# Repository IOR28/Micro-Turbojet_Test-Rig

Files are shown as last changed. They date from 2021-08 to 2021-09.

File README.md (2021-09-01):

# Micro-Turbojet Test Rig

This repository contains all the files created during my thesis, Test Rig Design for a Micro-Turbojet Engine. More information about these contents, designs and uses can be found in the document of the thesis.

Different parts of the test rig design where explored during the project, these are sepparated into folders with the same topic. The explanation of this organization and a brief explanation of each subproject can be found below.

### Contents

+ [StructureDesign](#structuredesign): Autodesk Inventor project
	+ Bellmouth: Parts, drawings and final files
	+ CommercialParts
	+ DesignedParts: Parts and drawings
+ [DataAcquisitionMCs](#dataacquisitionmcs): MPLAB X projects
	+ Pressure
	+ Temperature
	+ Thrust_Flow
+ [DataProcessingMaster](#dataprocessingmaster): Python files and classes
+ [PCBDesigns](#pcbdesigns): Autodesk Eagle projects
	+ RTD_conditioning
	+ System_control
	+ General_board

## [StructureDesign](./StructureDesign)

This folder contains the Autodesk Inventor files of the designed bench. the bench features both [commercial parts](./StructureDesign/CommercialParts) and [designed parts](./StructureDesign/DesignedParts). The design of a [bellmouth](./StructureDesign/Bellmouth) is also included.

All the designed components have their corresponding sketches in DWG, DXF and PDF formats so that they can be manufactured. The bellmouth is expected to be 3D printed, therefore, STL files are profided along with the sketches. The links to the commercial parts can be found in the budget of the project (document).

## [DataAcquisitionMCs](./DataAcquisitionMCs)

Here the MPLAB X projects can be found. Files are coded in C and are divided into 3 projects (each one corresponding to a microcontroller):
+ Pressure
+ Temperature
+ Thrust_Flow

In order to program the microcontrollers it is necessary to open the projects in the MPLAB X IDE, compile them and then transfer them to the mCs through a USB cable.

## [DataProcessingMaster](./DataProcessingMaster)

This folder contains the Python files and classes necessary to program the Raspberry Pi 4 that acts as master. This master connects to the microcontrollers in order to gather data and save it to a database.

All the files must be saved into the `Turbojet` folder (as they are organized) inside the Raspberry Pi 4 in order to function properly. More information about how the program works and how to modify it can be found in the document.

## [PCBDesigns](./PCBDesigns)

Three boards are designed to hold all the electronics together. Autodesk Eagle is used to create these and their projects can be found inside this folder. Boards are:
+ An RTD PT100 circuit board
+ A control board
+ A base board to hold all conditioning boards

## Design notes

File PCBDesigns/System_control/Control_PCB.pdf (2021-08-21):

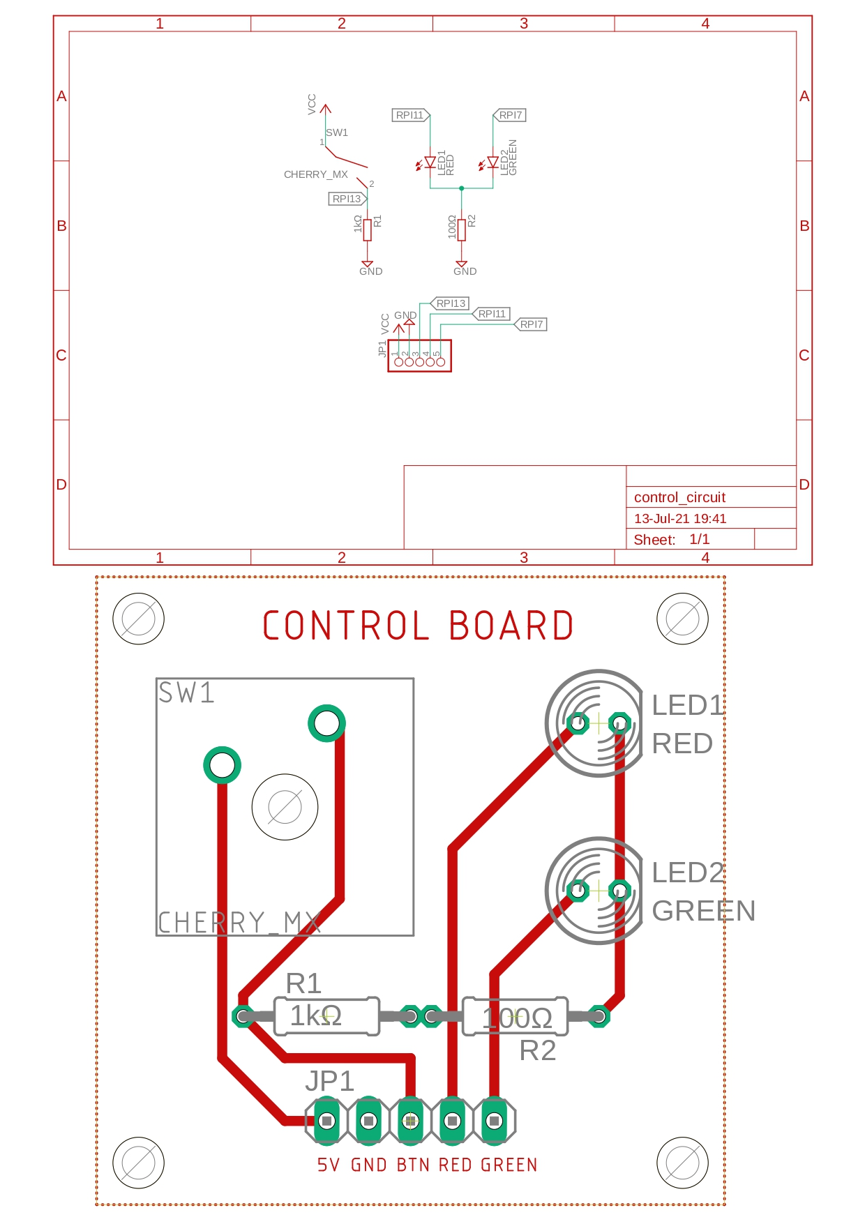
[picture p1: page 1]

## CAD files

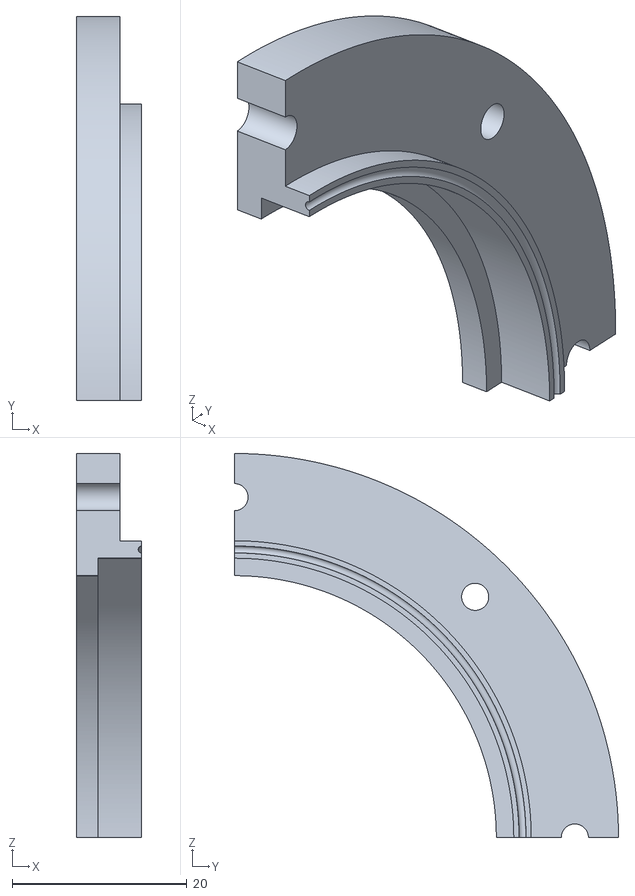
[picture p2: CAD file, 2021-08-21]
StructureDesign/Bellmouth/3DPrint/testprint_connector.stl
7.50 x 44.0 x 44.0

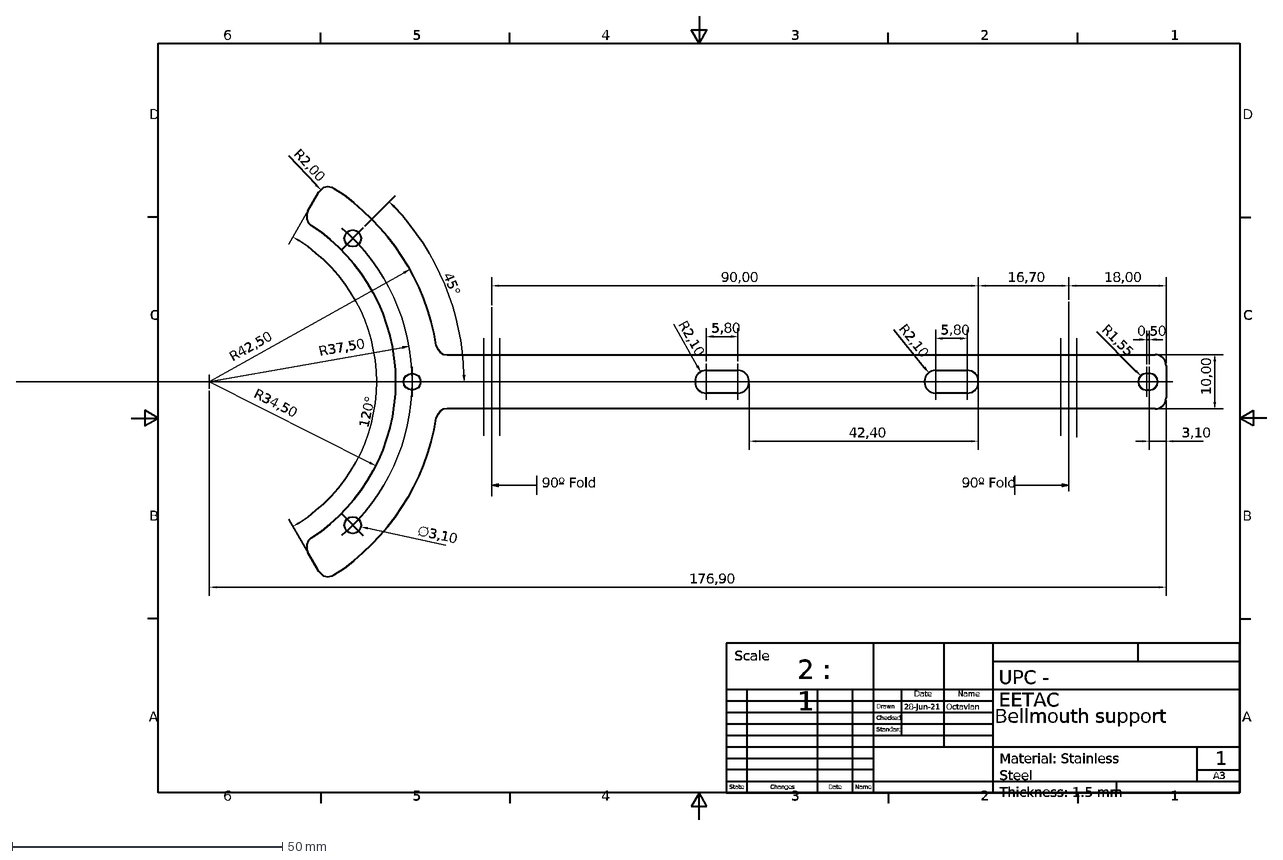
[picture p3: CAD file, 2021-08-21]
StructureDesign/Bellmouth/Drawings/DXF/Bellmouth_union.dxf
1
2
3
4
5
6
A
B
C
D
A3
Bellmouth support
28-Jun-21
Octavian
State
Changes
Date
Name
Drawn
Checked
Standard
5,80
120°
R34,50
R37,50
R42,50
45°
10,00
18,00
176,90
R2,10
3,10
0,50
R1,55
R2,00
∅3,10
90,00
16,70
42,40
Scale
2 : 1
UPC - EETAC
Material: Stainless Steel Thickness: 1.5 mm
90º Fold

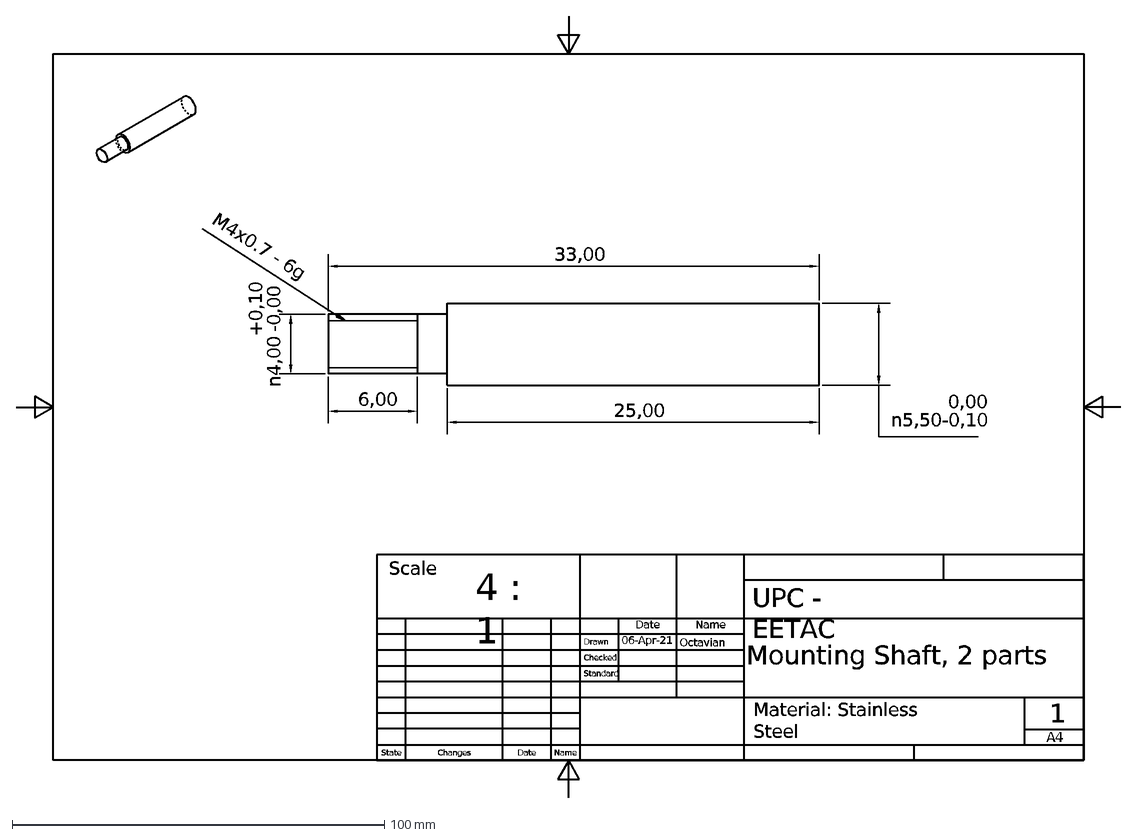
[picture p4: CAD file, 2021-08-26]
StructureDesign/DesignedParts/Drawings/DXF/Mounting_Shaft.dxf
1
A4
Mounting Shaft, 2 parts
06-Apr-21
Octavian
State
Changes
Date
Name
Drawn
Checked
Standard
33,00
25,00
6,00
M4x0.7 - 6g
Scale
4 : 1
UPC - EETAC
Material: Stainless Steel

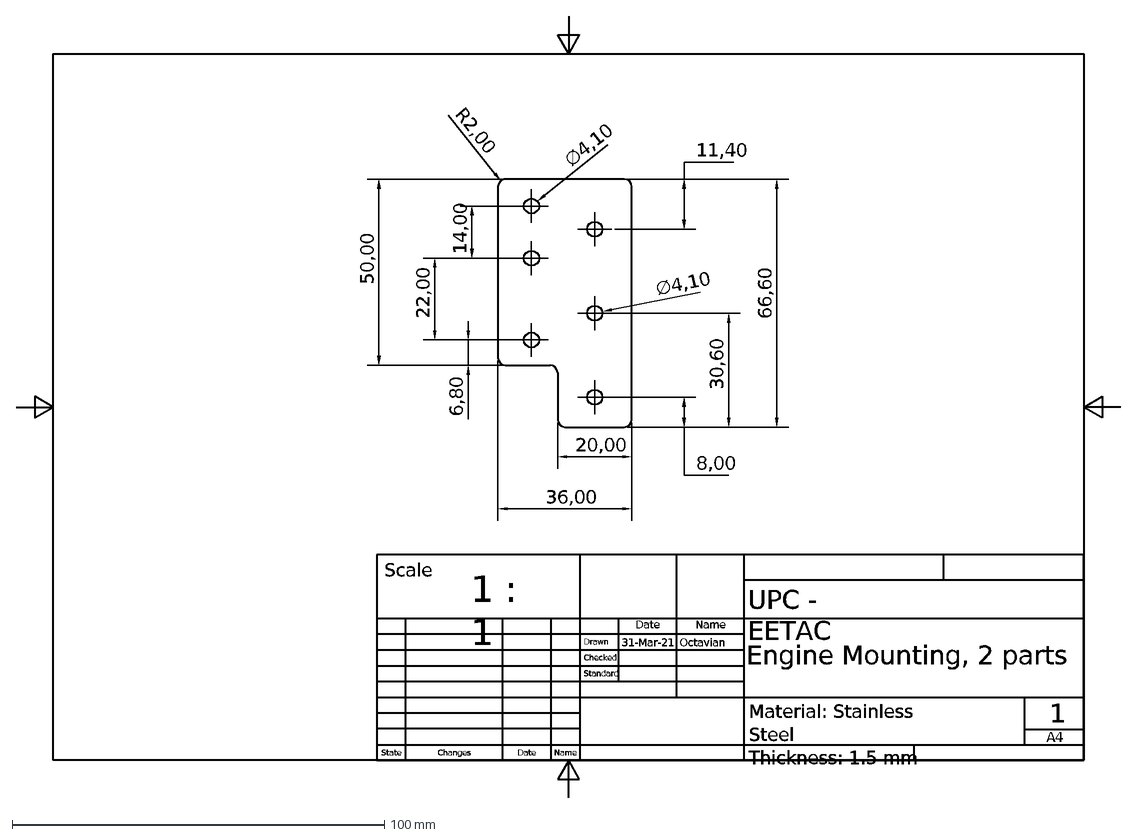
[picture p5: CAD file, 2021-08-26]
StructureDesign/DesignedParts/Drawings/DXF/Engine_Mounting.dxf
1
A4
Engine Mounting, 2 parts
31-Mar-21
Octavian
State
Changes
Date
Name
Drawn
Checked
Standard
66,60
50,00
R2,00
14,00
22,00
36,00
20,00
6,80
11,40
∅4,10
30,60
8,00
Scale
1 : 1
UPC - EETAC
Material: Stainless Steel Thickness: 1.5 mm

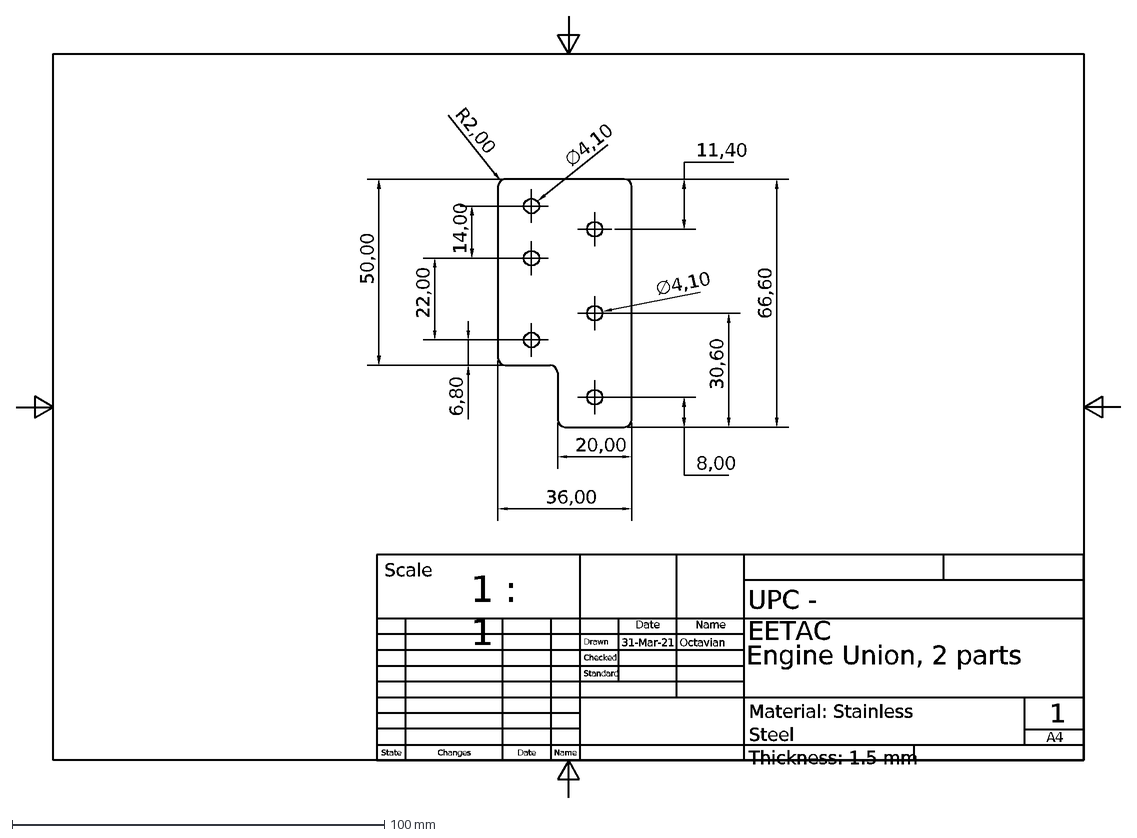
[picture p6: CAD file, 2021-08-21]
StructureDesign/DesignedParts/Drawings/DXF/Engine_Union.dxf
1
A4
Engine Union, 2 parts
31-Mar-21
Octavian
State
Changes
Date
Name
Drawn
Checked
Standard
66,60
50,00
R2,00
14,00
22,00
36,00
20,00
6,80
11,40
∅4,10
30,60
8,00
Scale
1 : 1
UPC - EETAC
Material: Stainless Steel Thickness: 1.5 mm

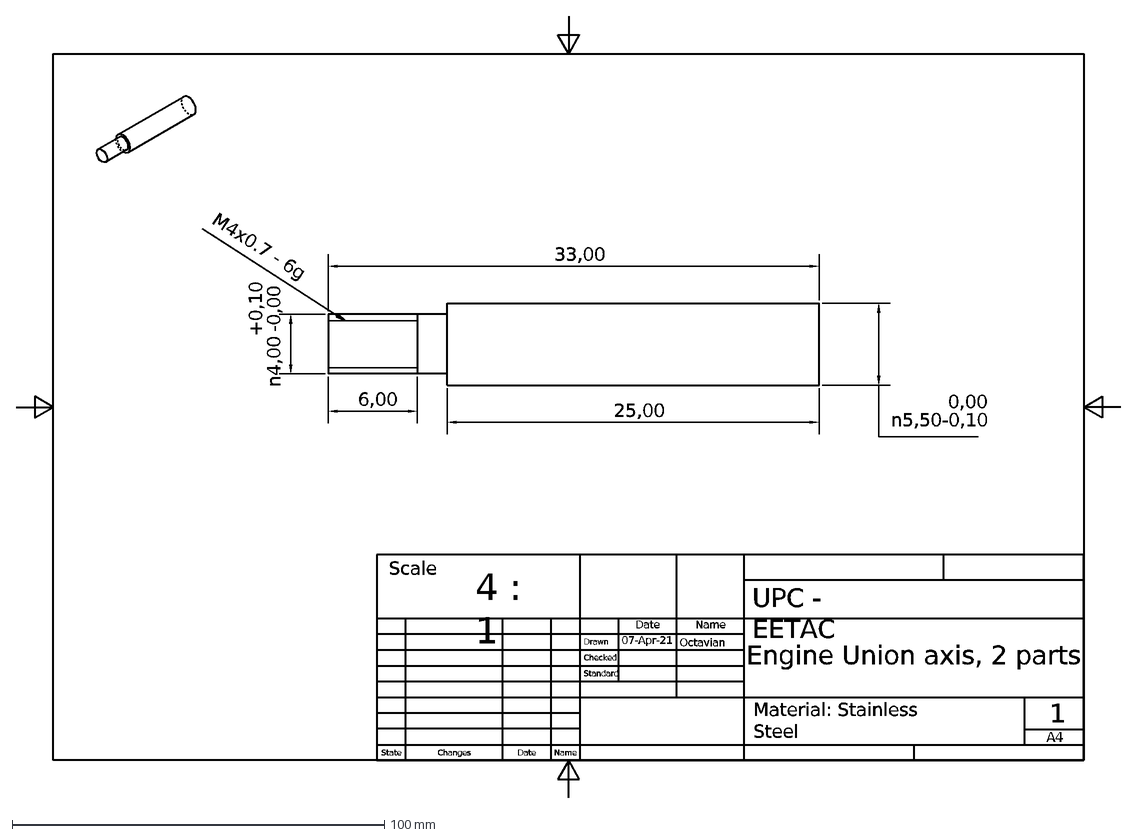
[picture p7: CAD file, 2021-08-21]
StructureDesign/DesignedParts/Drawings/DXF/Union_Axis.dxf
1
A4
Engine Union axis, 2 parts
07-Apr-21
Octavian
State
Changes
Date
Name
Drawn
Checked
Standard
33,00
25,00
6,00
M4x0.7 - 6g
Scale
4 : 1
UPC - EETAC
Material: Stainless Steel

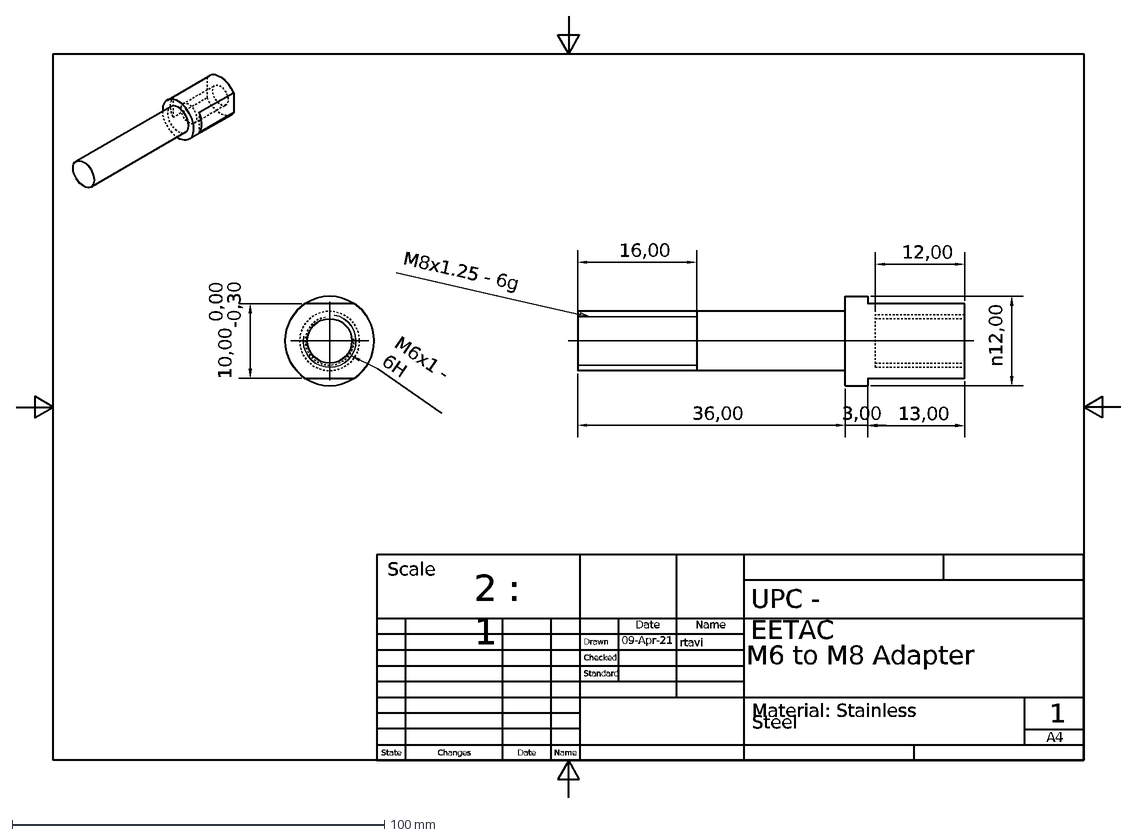
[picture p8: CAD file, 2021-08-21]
StructureDesign/DesignedParts/Drawings/DXF/M6_M8_Adapter.dxf
1
A4
M6 to M8 Adapter
09-Apr-21
rtavi
State
Changes
Date
Name
Drawn
Checked
Standard
10,00 0,00^-0,30
M6x1 - 6H
36,00
3,00
13,00
12,00
16,00
M8x1.25 - 6g
Scale
2 : 1
UPC - EETAC
Material: Stainless Steel

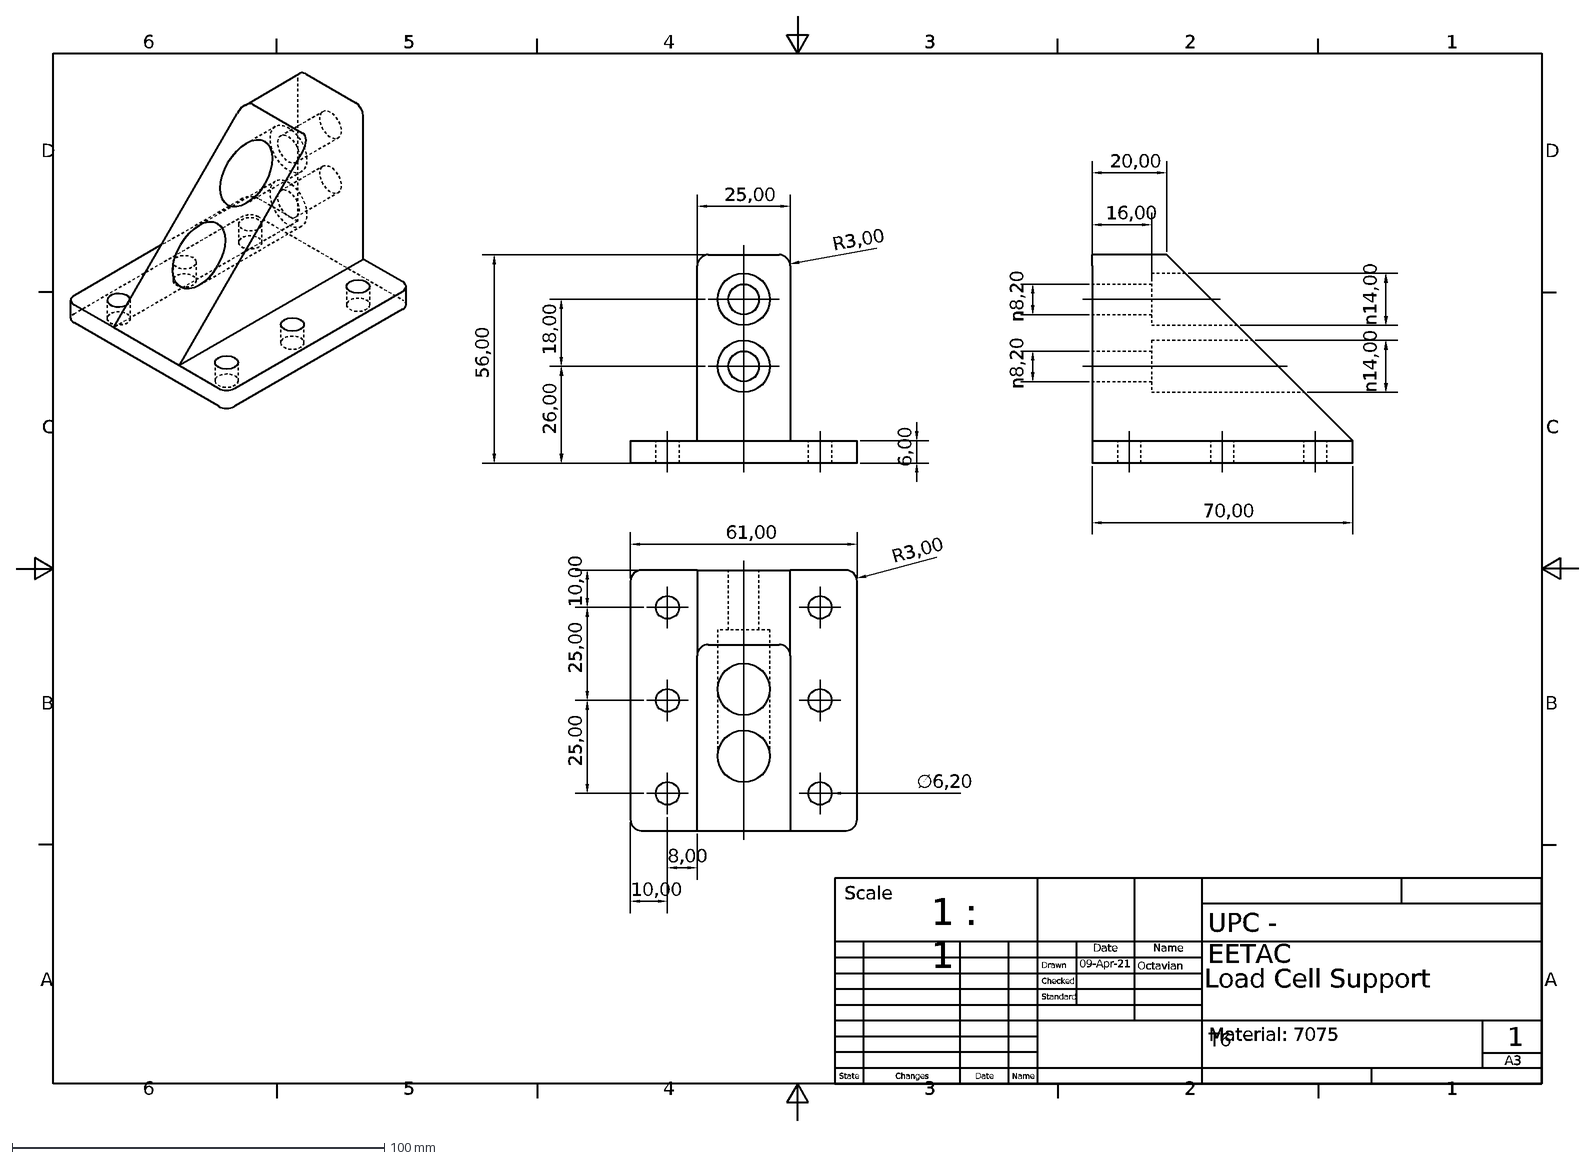
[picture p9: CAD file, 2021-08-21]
StructureDesign/DesignedParts/Drawings/DXF/LC_Support.dxf
1
2
3
4
5
6
A
B
C
D
A3
Load Cell Support
09-Apr-21
Octavian
State
Changes
Date
Name
Drawn
Checked
Standard
56,00
6,00
25,00
20,00
70,00
R3,00
10,00
8,00
26,00
18,00
∅6,20
16,00
61,00
1 : 1
UPC - EETAC
Scale
Material: 7075 T6

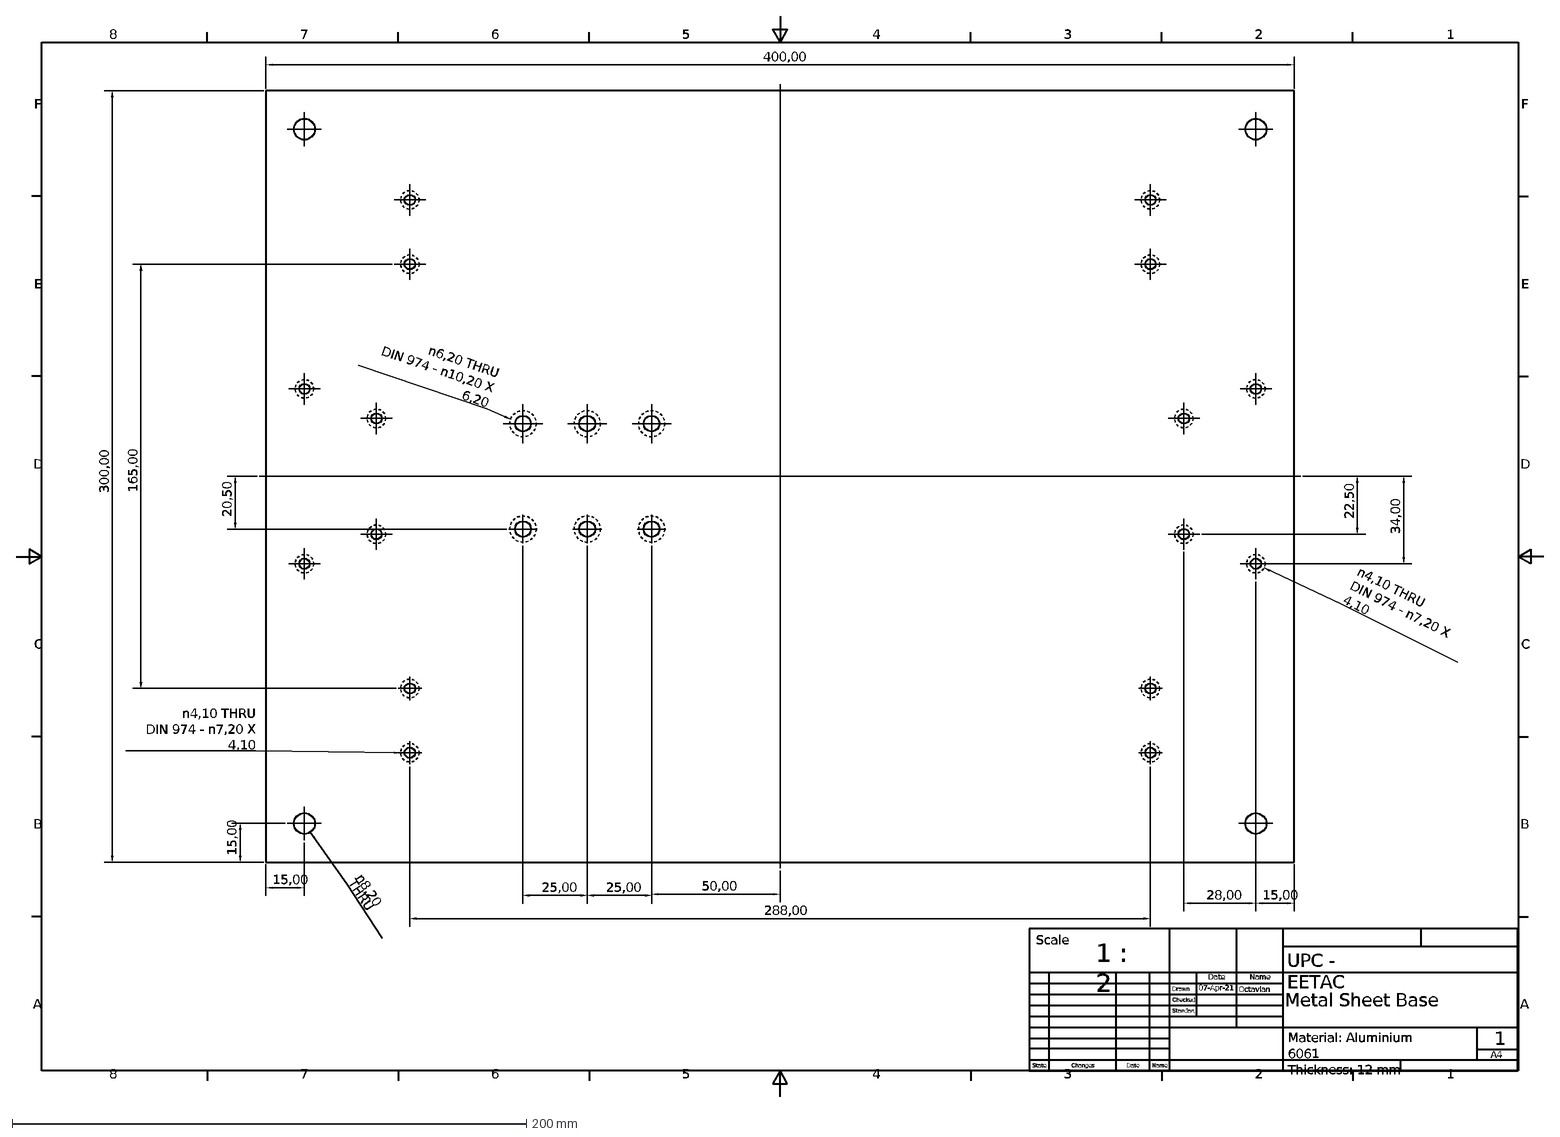
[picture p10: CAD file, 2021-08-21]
StructureDesign/DesignedParts/Drawings/DXF/Base.dxf
1
2
3
4
5
6
7
8
A
B
C
D
E
F
Metal Sheet Base
07-Apr-21
Octavian
State
Changes
Date
Name
Drawn
Checked
Standard
300,00
400,00
15,00
34,00
22,50
28,00
50,00
25,00
20,50
288,00
165,00
Scale
1 : 2
UPC - EETAC
Material: Aluminium 6061 Thickness: 12 mm
A4

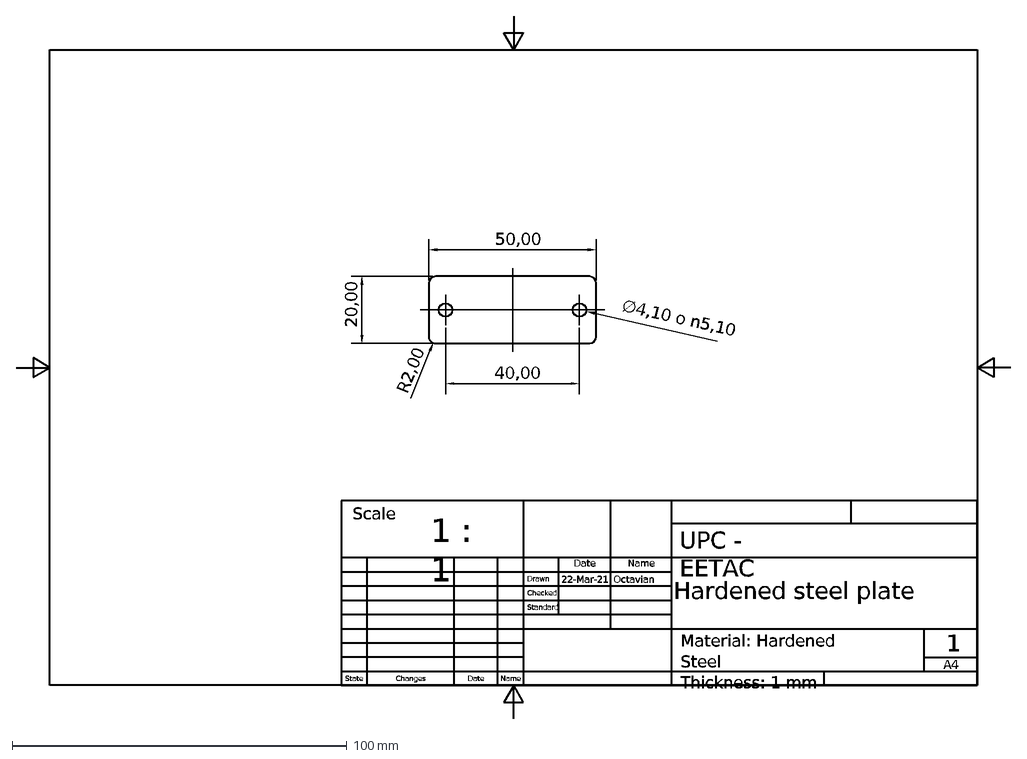
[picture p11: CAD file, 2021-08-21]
StructureDesign/DesignedParts/Drawings/DXF/Hardened_Plate.dxf
1
A4
Hardened steel plate
22-Mar-21
Octavian
State
Changes
Date
Name
Drawn
Checked
Standard
20,00
50,00
40,00
R2,00
Scale
1 : 1
UPC - EETAC
Material: Hardened Steel Thickness: 1 mm

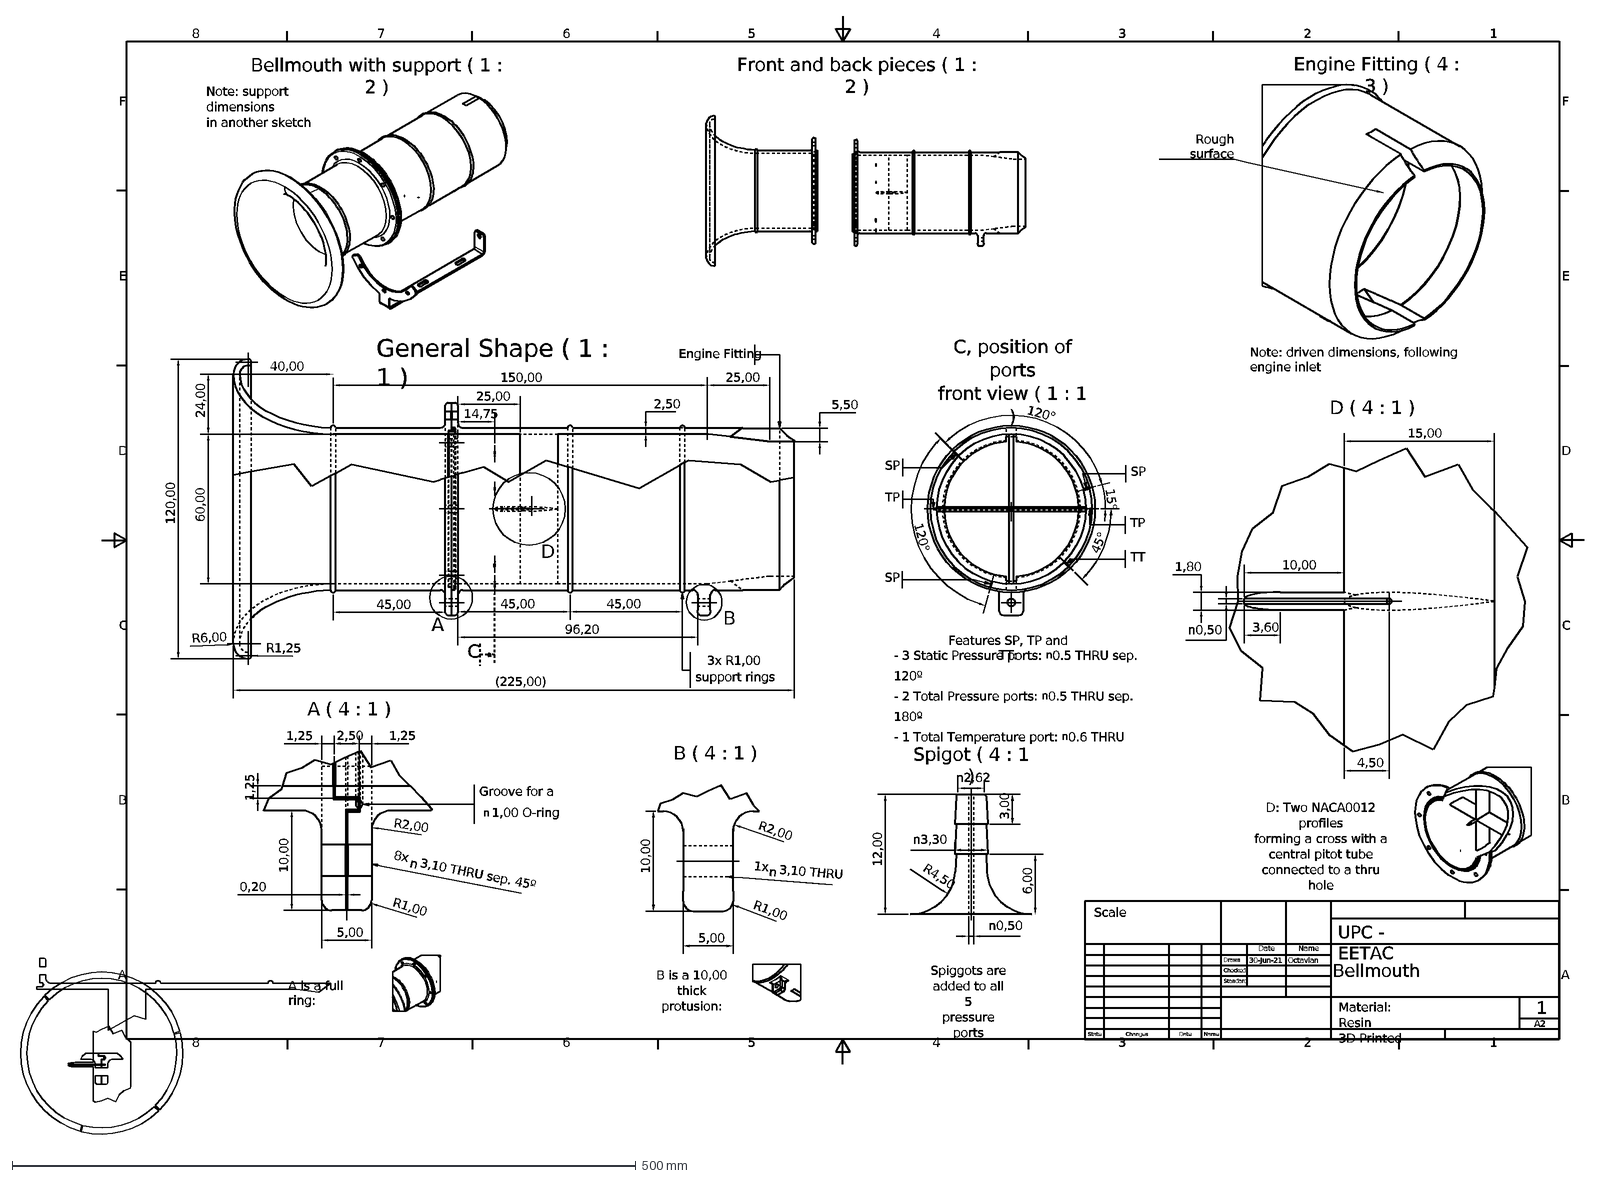
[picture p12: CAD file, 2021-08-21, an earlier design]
StructureDesign/Bellmouth/Drawings/DXF/OldVersions/Bellmouth.xxxx.dxf
1
2
3
4
5
6
7
8
A
B
C
D
E
F
A2
Bellmouth
30-Jun-21
Octavian
State
Changes
Date
Name
Drawn
Checked
Standard
25,00
2,50
5,50
40,00
24,00
General Shape ( 1 : 1 )
Engine Fitting
Engine Fitting ( 4 : 3 )
Rough surface
Note: driven dimensions, following engine inlet
96,20
A ( 4 : 1 )
5,00
10,00
R1,00
R2,00
8x
3,10 THRU sep. 45º
B ( 4 : 1 )
1x
3,10 THRU
A is a full ring:
B is a 10,00 thick protusion:
D ( 4 : 1 )
1,80
3,60
D: Two NACA0012 profiles forming a cross with a central pitot tube connected to a thru hole
Spigot ( 4 : 1 )
12,00
3,00
6,00
R4,50
Spiggots are added to all 5 pressure ports
Bellmouth with support ( 1 : 2 )
Note: support dimensions in another sketch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

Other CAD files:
StructureDesign/Bellmouth/Drawings/DXF/Bellmouth.dxf
StructureDesign/Bellmouth/Bellmouth.ipt
StructureDesign/Bellmouth/Bellmouth_union.ipt
StructureDesign/Bellmouth/Drawings/DWG/Bellmouth.dwg
StructureDesign/Bellmouth/Drawings/DWG/Bellmouth_union.dwg
StructureDesign/Bellmouth/Parts/Back_piece.ipt
StructureDesign/Bellmouth/Parts/Front_piece.ipt
StructureDesign/Bellmouth/Parts/spiggot_0.5mm_round.ipt
StructureDesign/CommercialParts/Bearing_LUCS8.ipt
StructureDesign/CommercialParts/Bracket.ipt
StructureDesign/CommercialParts/Bracket_20X40.ipt
StructureDesign/CommercialParts/Engine.ipt
StructureDesign/CommercialParts/Engine_data.ipt
StructureDesign/CommercialParts/Horizontal_profile_260mm.ipt
StructureDesign/CommercialParts/Load_Cell.ipt
StructureDesign/CommercialParts/Screws/m6-nut.ipt
StructureDesign/CommercialParts/Screws/m6-washer.ipt
StructureDesign/CommercialParts/Screws/m6x25.ipt
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

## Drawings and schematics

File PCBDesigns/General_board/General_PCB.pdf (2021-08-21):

A

A

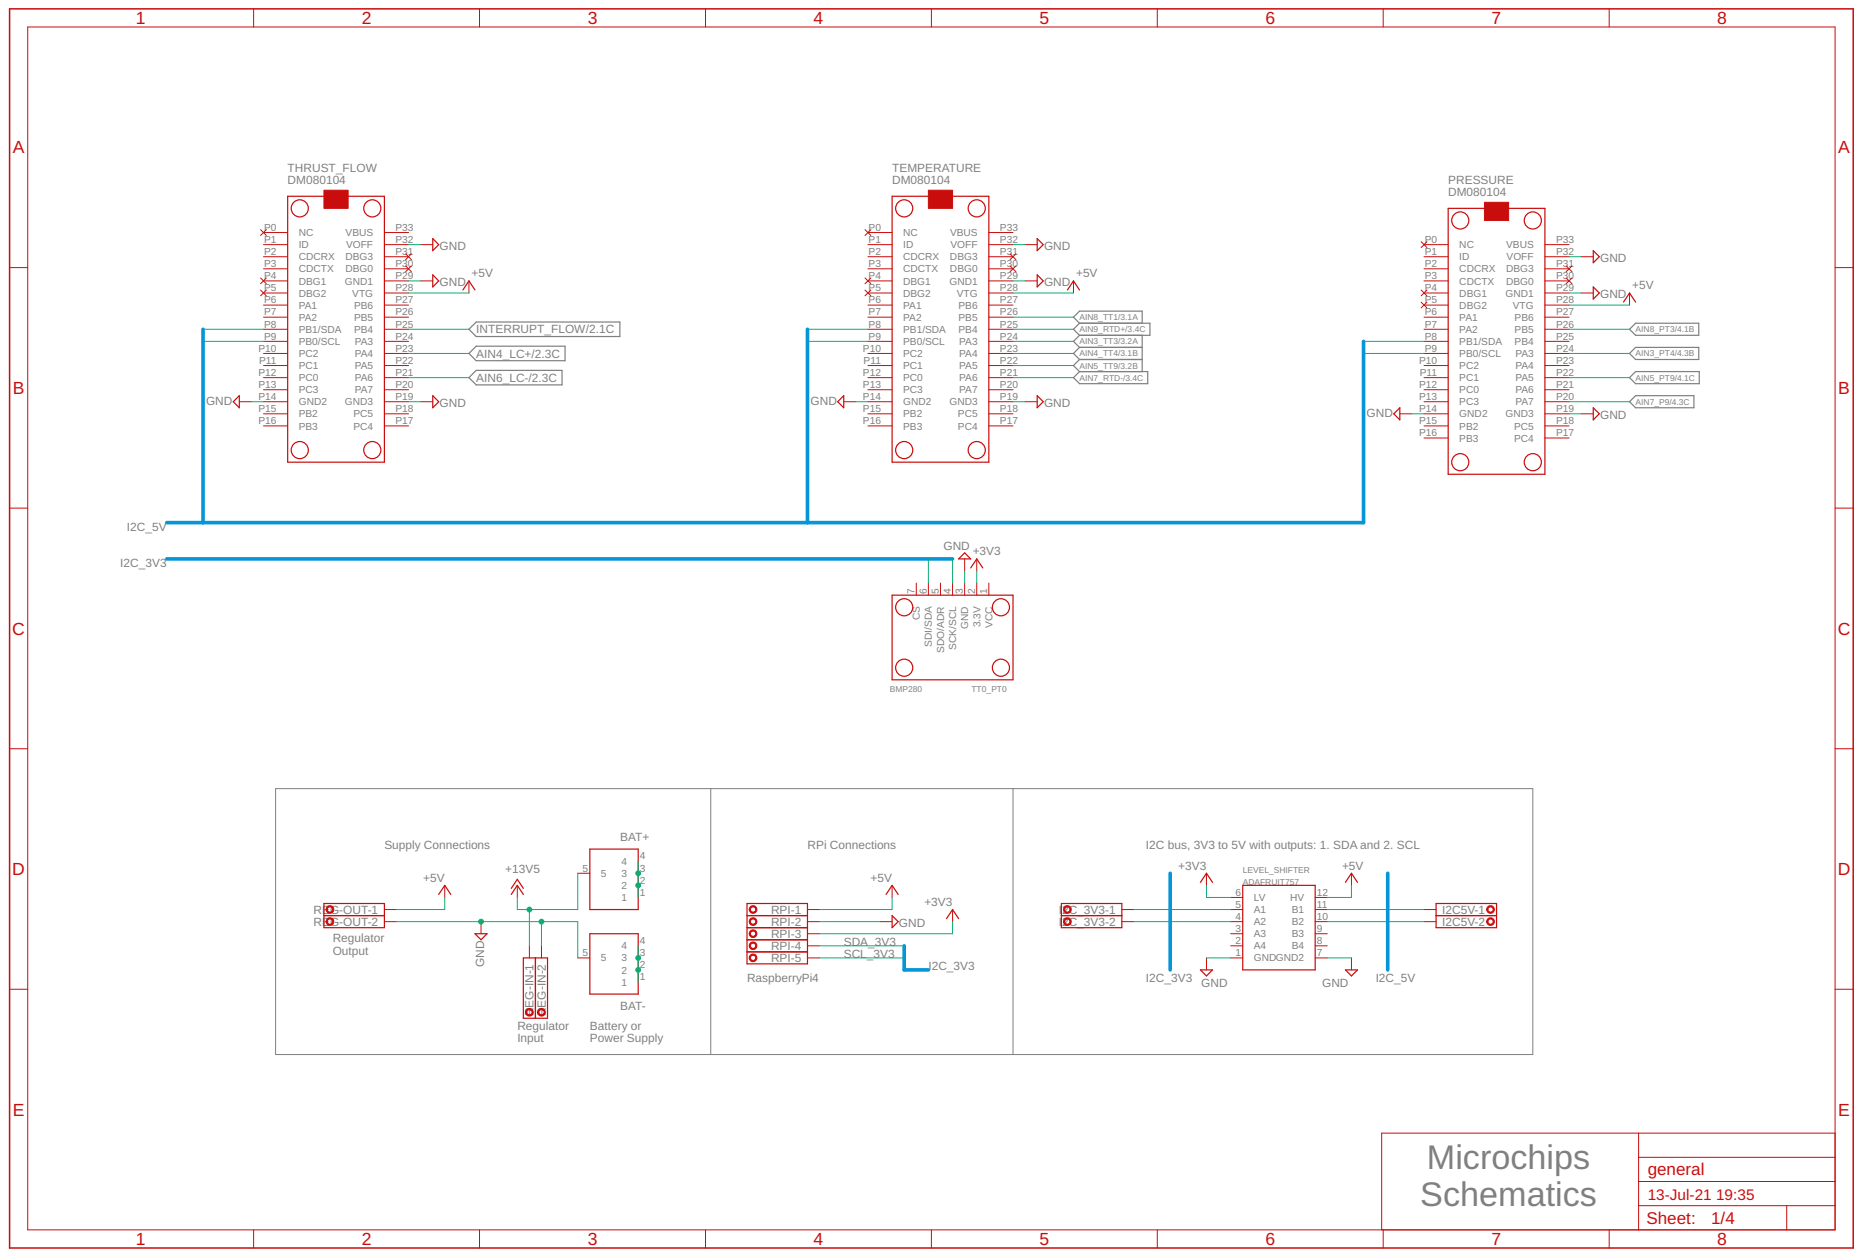
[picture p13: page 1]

RPi Connections Regulator Output

REG-IN-1 REG-IN-2

Battery or Power Supply

Microchips Schematics

Sheet: 1/4

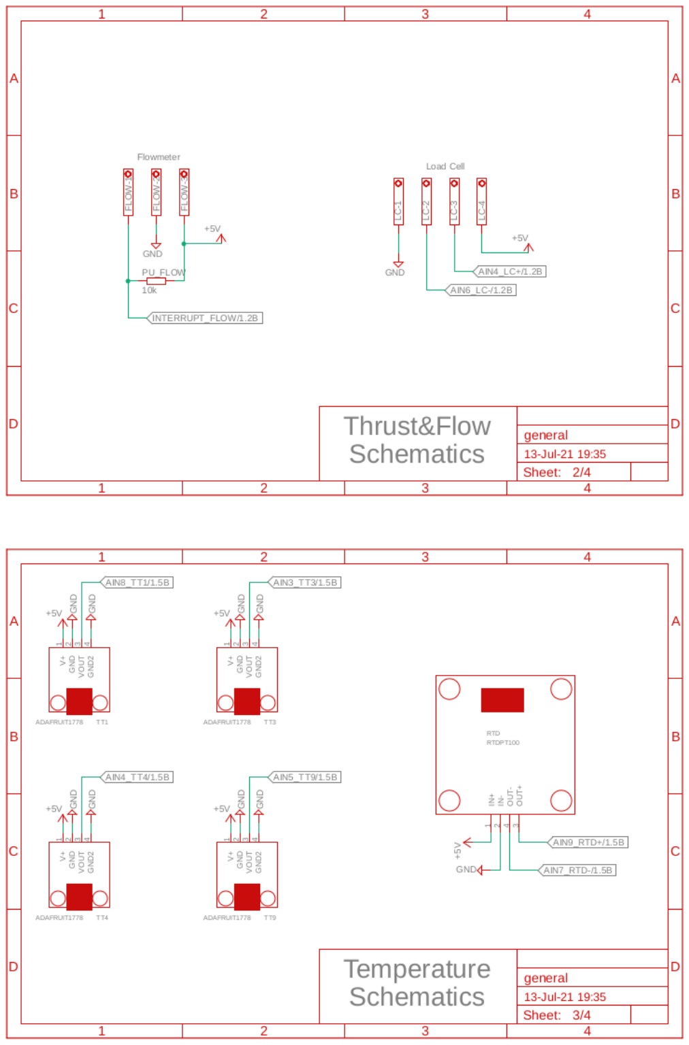
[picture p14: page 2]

A

A

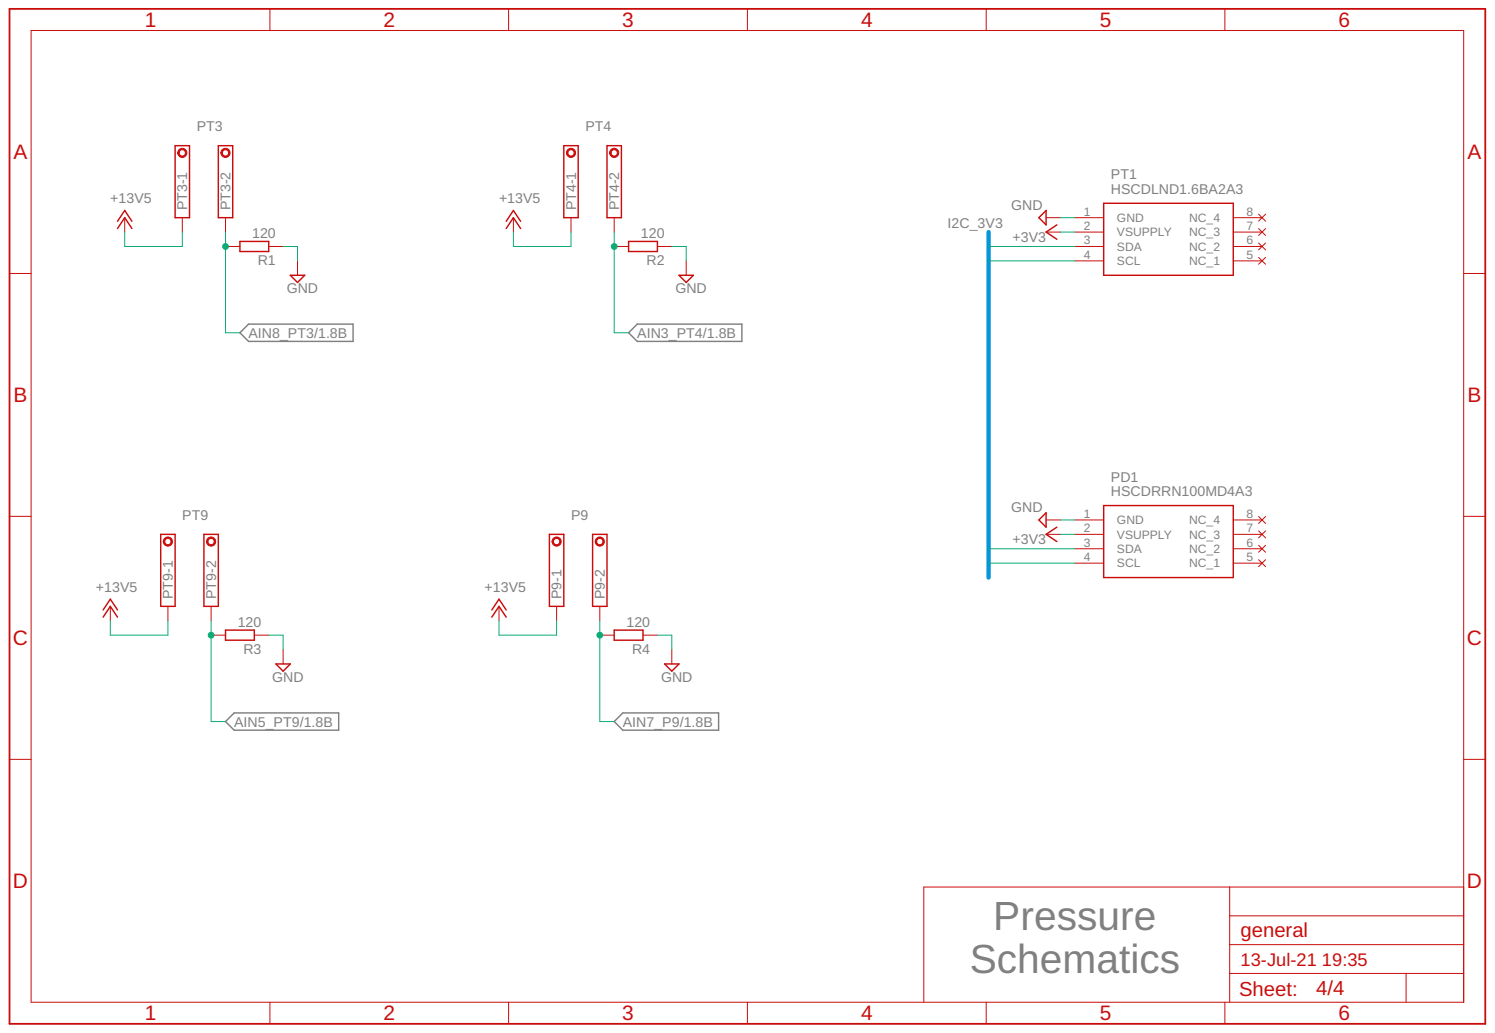
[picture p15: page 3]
GND; HSCDLND1.6BA2A3; HSCDRRN100MD4A3; VSUPPLY; SDA; SCL; AIN8_PT3/1.8B; AIN3_PT4/1.8B; AIN5_PT9/1.8B; AIN7_P9/1.8B; general; 13-Jul-21 19:35

Pressure Schematics

Sheet: 4/4

BAT+ BAT- FLOW I2C5V I2C_3V3 | LC LEVEL_SHIFTER | P⁹ | PD¹ PRESSURE | PT1 PT3 | PT4 | PT9 PU_FLOW R1 | R2 | R3 | R4 | REG⁻IN REG⁻OUT RPI | RTD TEMPERATURE THRUST_FLOW | TT0_PT0 TT9 | TT4 | TT3 | TT1

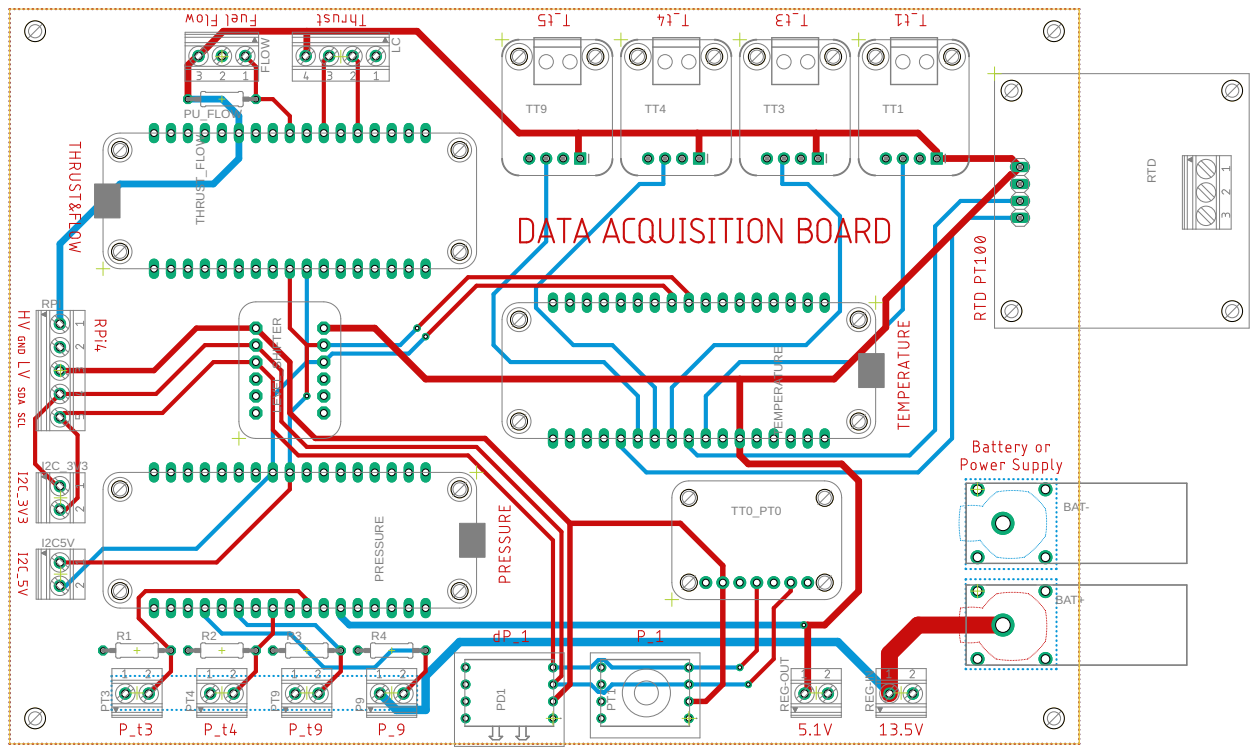
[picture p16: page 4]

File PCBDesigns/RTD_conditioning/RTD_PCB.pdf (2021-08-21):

A

A

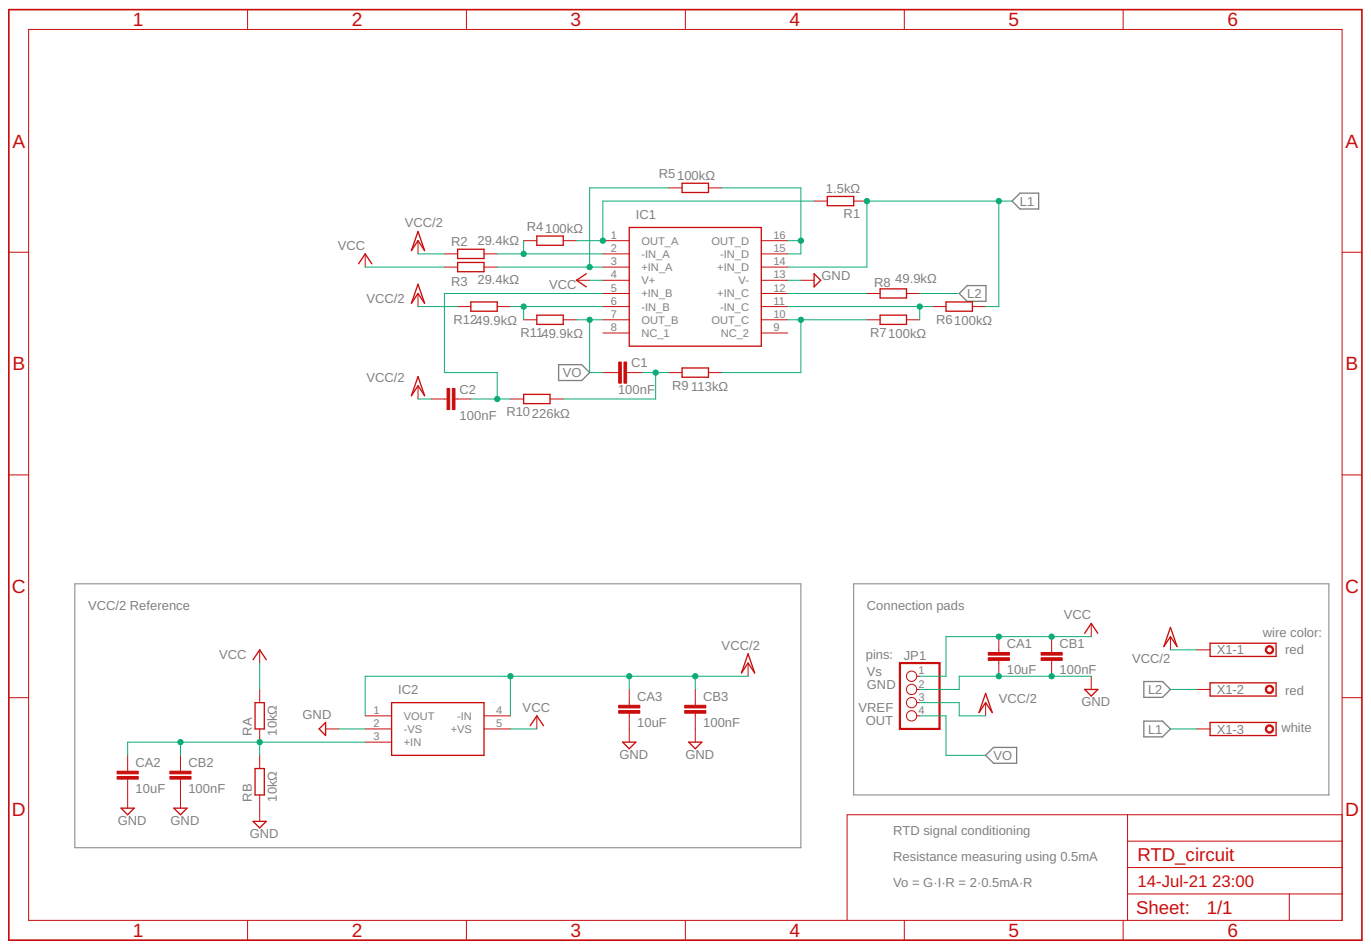
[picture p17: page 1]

Connection pads pins: Vs GND

RTD signal conditioning Resistance measuring using 0.5mA Vo = G·I·R = 2·0.5mA·R

Sheet: 1/1

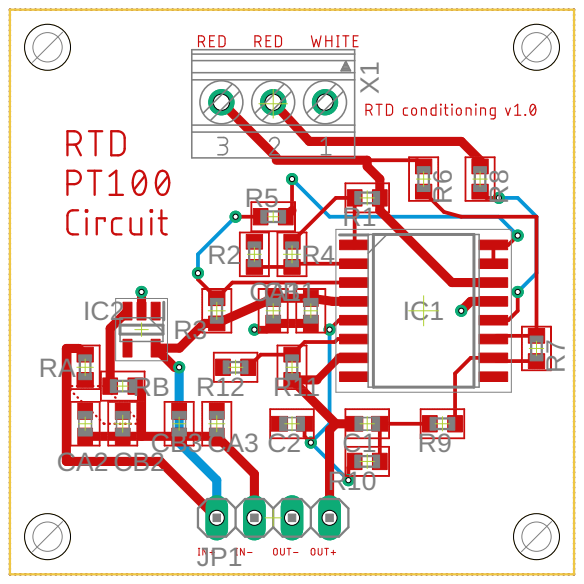
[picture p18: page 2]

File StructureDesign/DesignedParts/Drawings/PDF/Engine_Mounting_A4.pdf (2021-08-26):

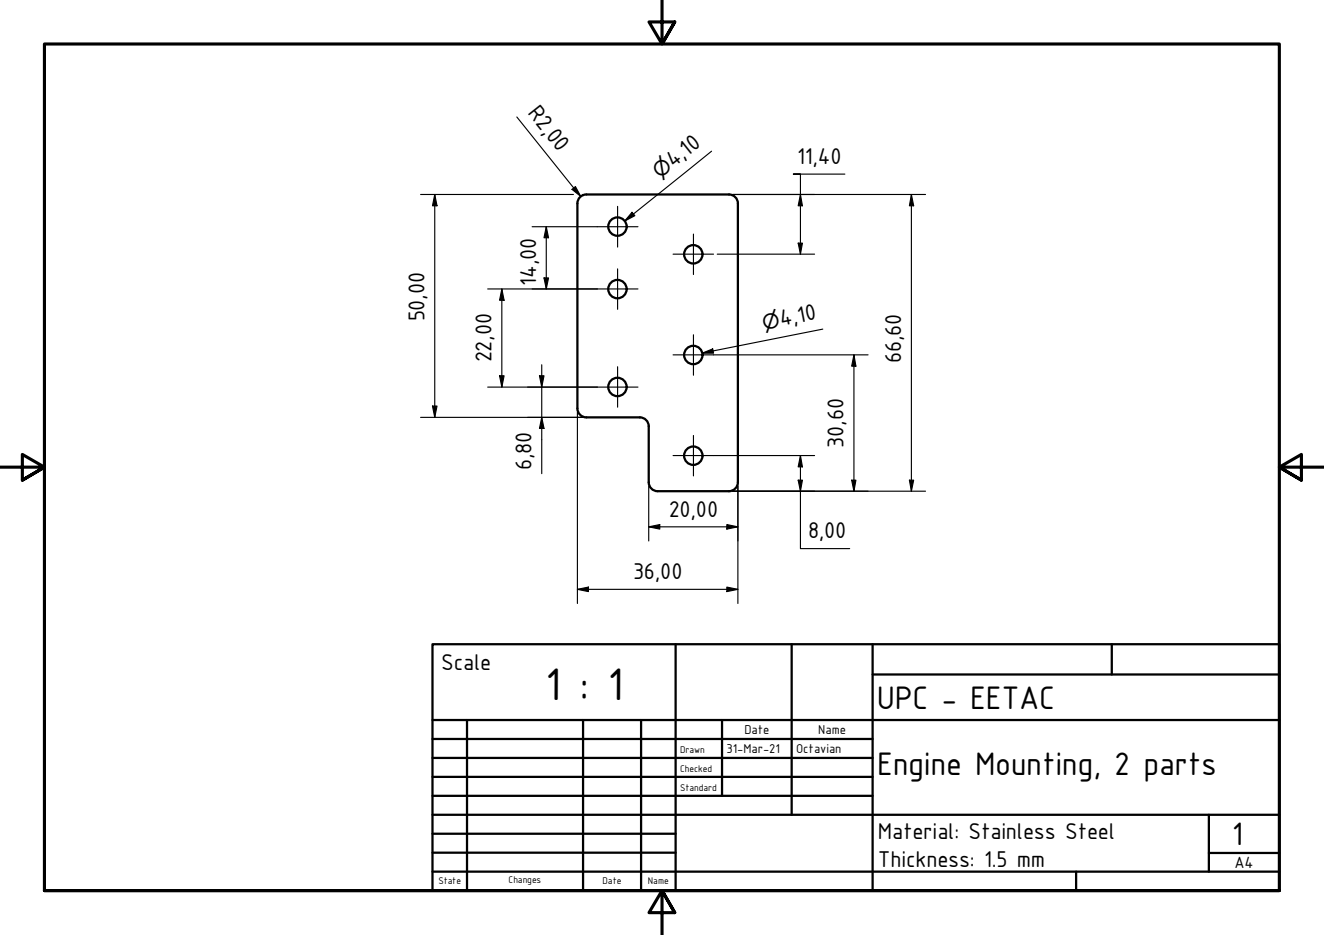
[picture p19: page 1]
UPC - EETAC

Date | Name | Engine Mounting, 2 parts

Drawn | 31-Mar-21 | Octavian

Checked

Standard

Material: Stainless Steel
Thickness: 1.5 mm

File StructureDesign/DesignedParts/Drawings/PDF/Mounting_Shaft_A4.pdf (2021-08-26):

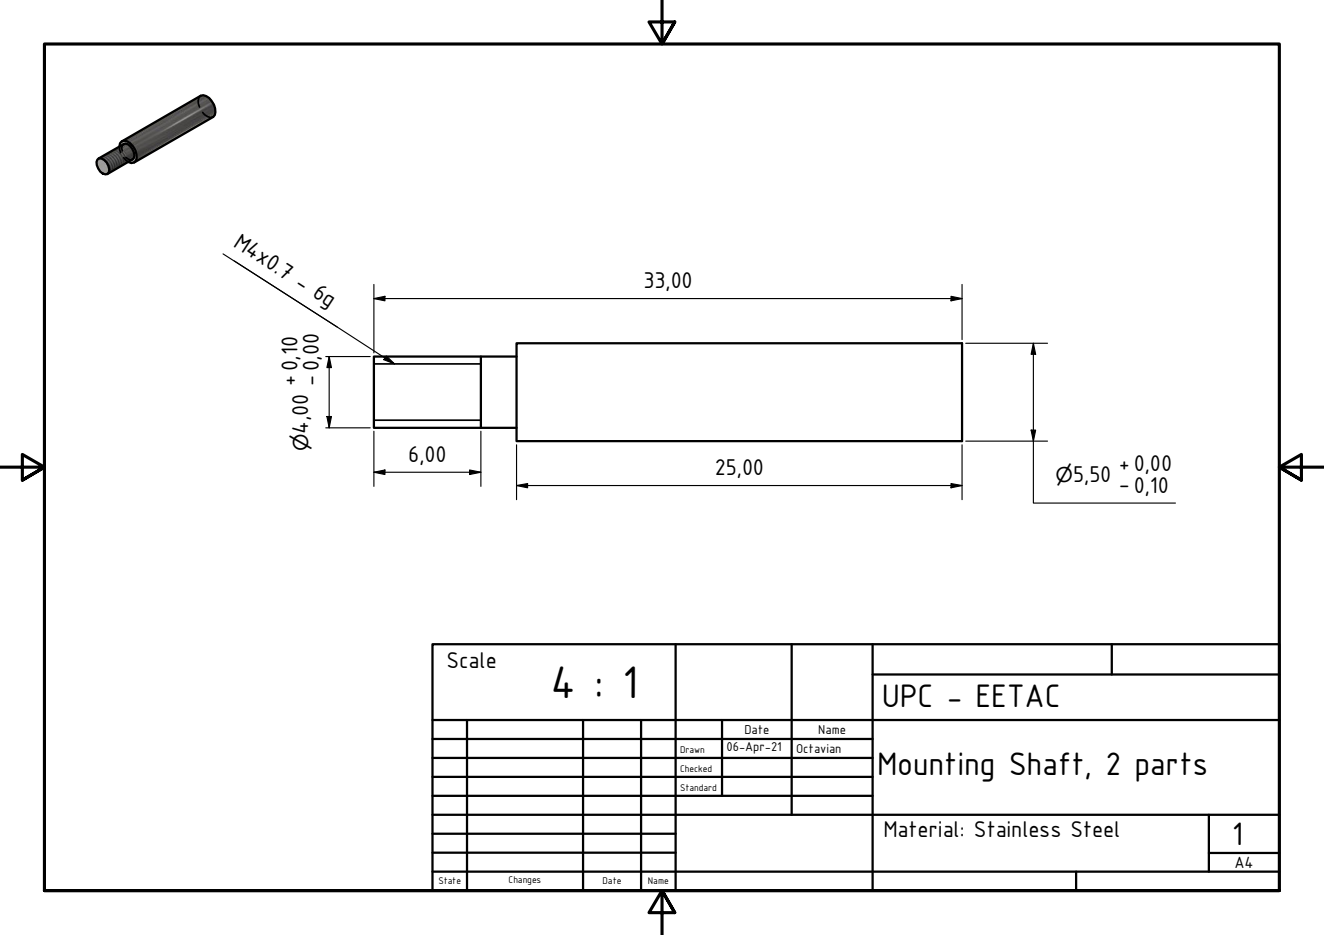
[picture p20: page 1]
UPC - EETAC

Date | Name | Mounting Shaft, 2 parts

Drawn | 06-Apr-21 | Octavian

Checked

Standard

Material: Stainless Steel

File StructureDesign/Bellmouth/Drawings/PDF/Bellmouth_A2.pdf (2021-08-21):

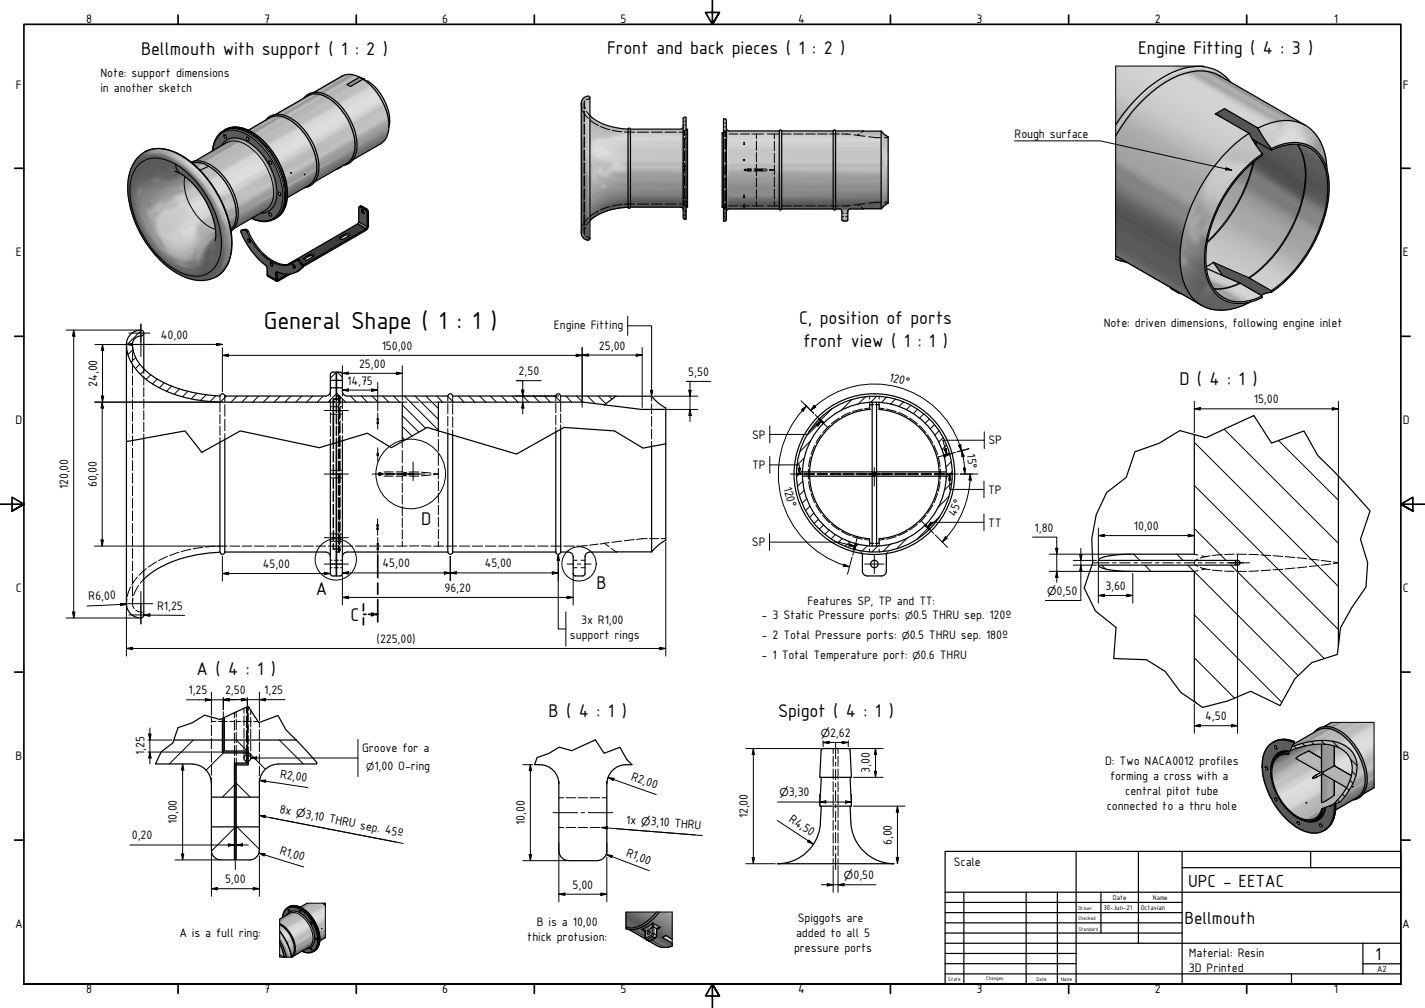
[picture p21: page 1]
General Shape ( 1 : 1 ); Engine Fitting; Engine Fitting ( 4 : 3 ); Rough surface; B is a 10,00 thick protusion:; Spigot ( 4 : 1 ); 3x R1,00 support rings; Groove for a; UPC - EETAC; Material: Resin 3D Printed

Front and back pieces ( 1 : 2 )

Bellmouth with support ( 1 : 2 )

Note: support dimensions
in another sketch

C, position of ports
front view ( 1 : 1 )

Note: driven dimensions, following engine inlet

Features SP, TP and TT:

- 3 Static Pressure ports: 0.5 THRU sep. 120u
- 2 Total Pressure ports: 0.5 THRU sep. 180u
- 1 Total Temperature port: 0.6 THRU

D: Two NACA0012 profiles
forming a cross with a
central pitot tube
connected to a thru hole

Scale

Date | Name | Bellmouth

Drawn | 30-Jun-21 | Octavian

Spiggots are
added to all 5
pressure ports

Checked

A is a full ring:

Standard

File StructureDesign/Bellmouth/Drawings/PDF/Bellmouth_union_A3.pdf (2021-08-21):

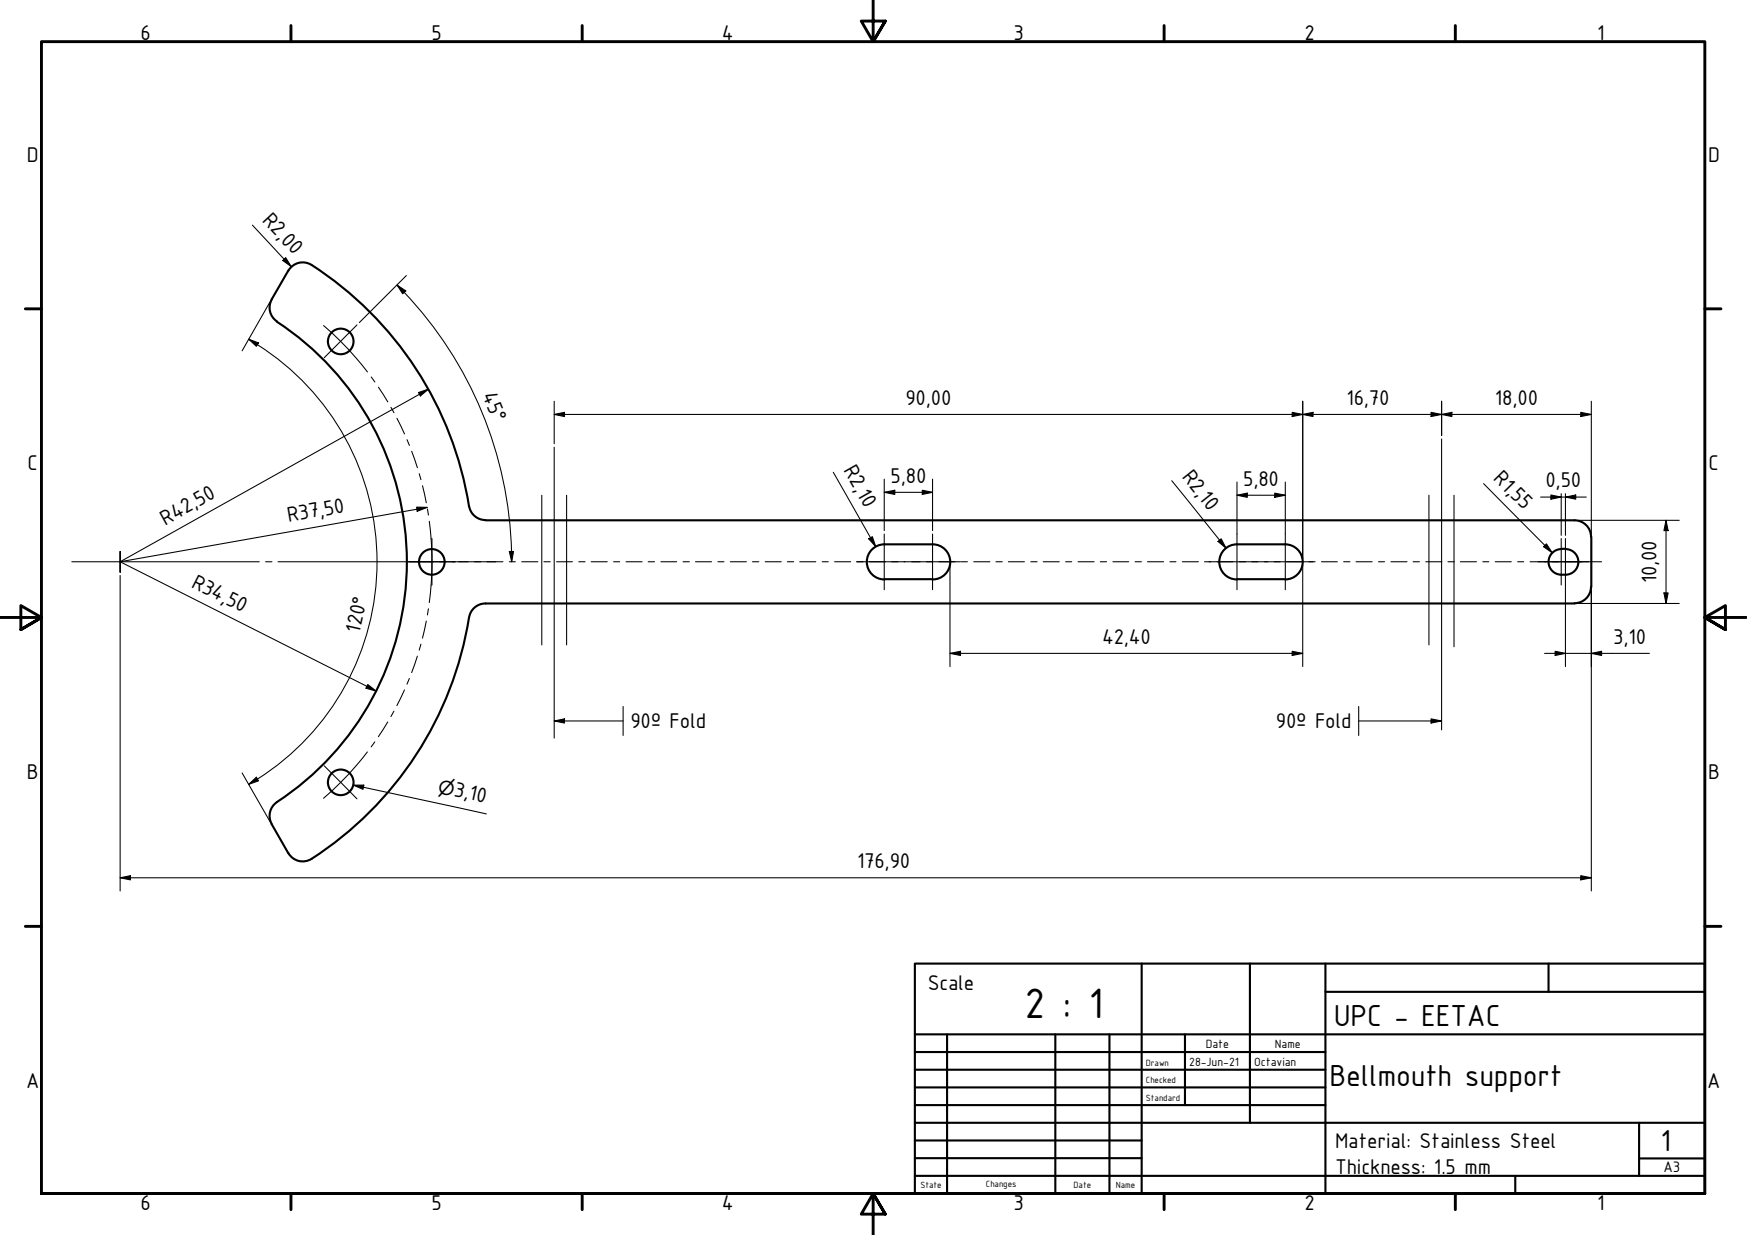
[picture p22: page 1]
UPC - EETAC; 90u Fold

Date | Name | Bellmouth support

Drawn | 28-Jun-21 | Octavian

Checked

Standard

Material: Stainless Steel
Thickness: 1.5 mm

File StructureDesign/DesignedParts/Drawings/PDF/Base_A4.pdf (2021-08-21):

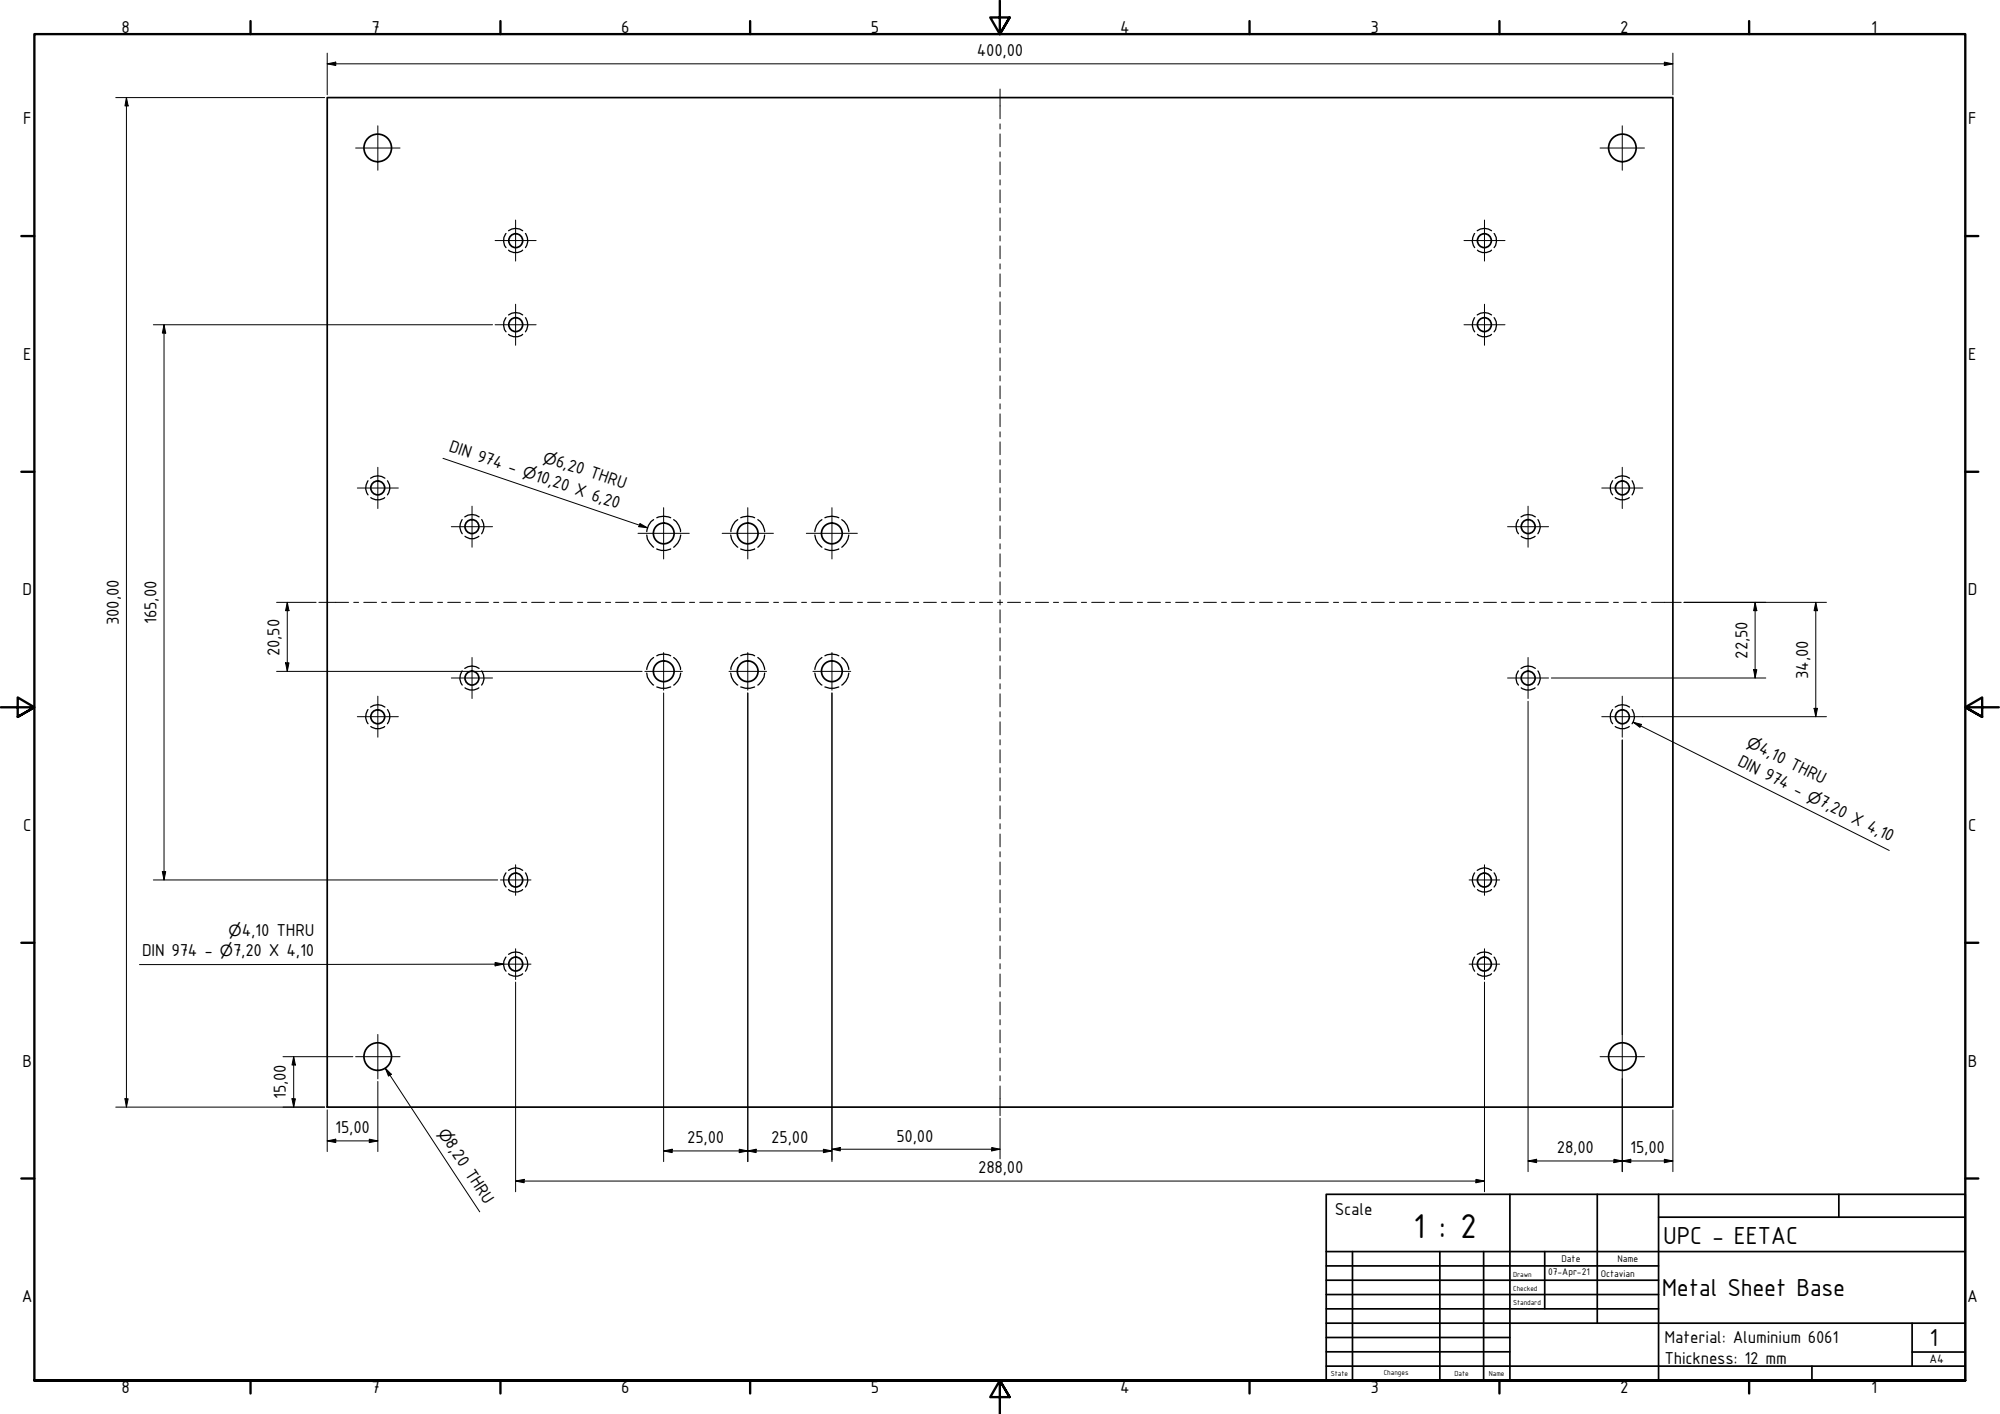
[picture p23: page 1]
State; Changes; Date; Name; Drawn; Checked; Standard; 07-Apr-21; Octavian; THRU; P4,10 THRU DIN 974; P4,10 THRU DIN 974 - P7,20 X 4,10; P6,20 THRU DIN 974 - P10,20 X 6,20; Scale; UPC - EETAC; Material: Aluminium 6061; Thickness: 12 mm

Metal Sheet Base

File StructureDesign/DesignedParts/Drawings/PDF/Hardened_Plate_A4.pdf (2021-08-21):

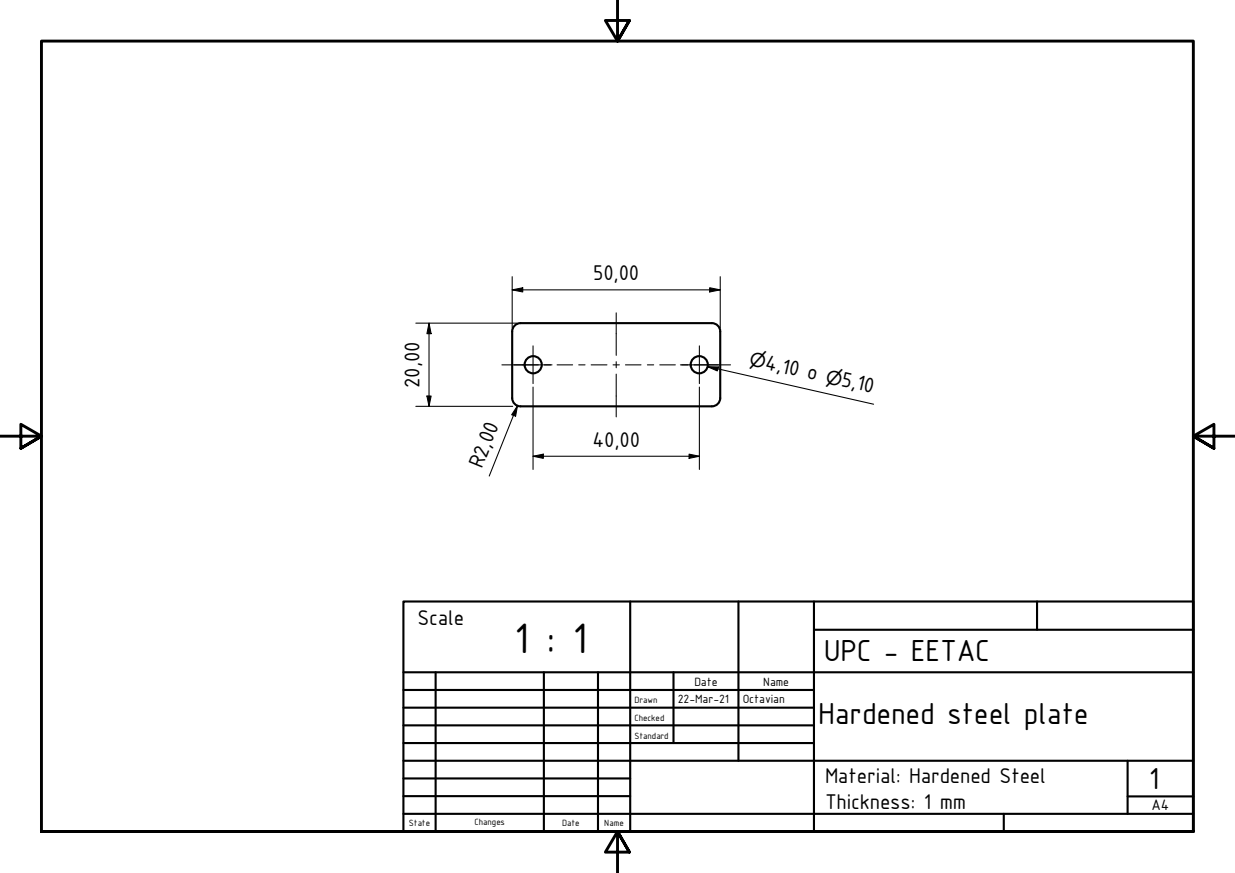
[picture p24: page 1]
UPC - EETAC

Date | Name | Hardened steel plate

Drawn | 22-Mar-21 | Octavian

Checked

Standard

Material: Hardened Steel
Thickness: 1 mm

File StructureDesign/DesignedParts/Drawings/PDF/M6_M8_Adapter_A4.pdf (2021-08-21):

UPC - EETAC

Date | Name | M6 to M8 Adapter

Drawn | 09-Apr-21 | rtavi

Checked

Standard

Material: Stainless Steel

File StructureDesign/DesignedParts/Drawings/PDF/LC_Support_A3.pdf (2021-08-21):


D r a w n | 0 9 -A p r -2 1 | O c t a via n

M a t e ria l: 7 0 7 5 T 6 | 1A

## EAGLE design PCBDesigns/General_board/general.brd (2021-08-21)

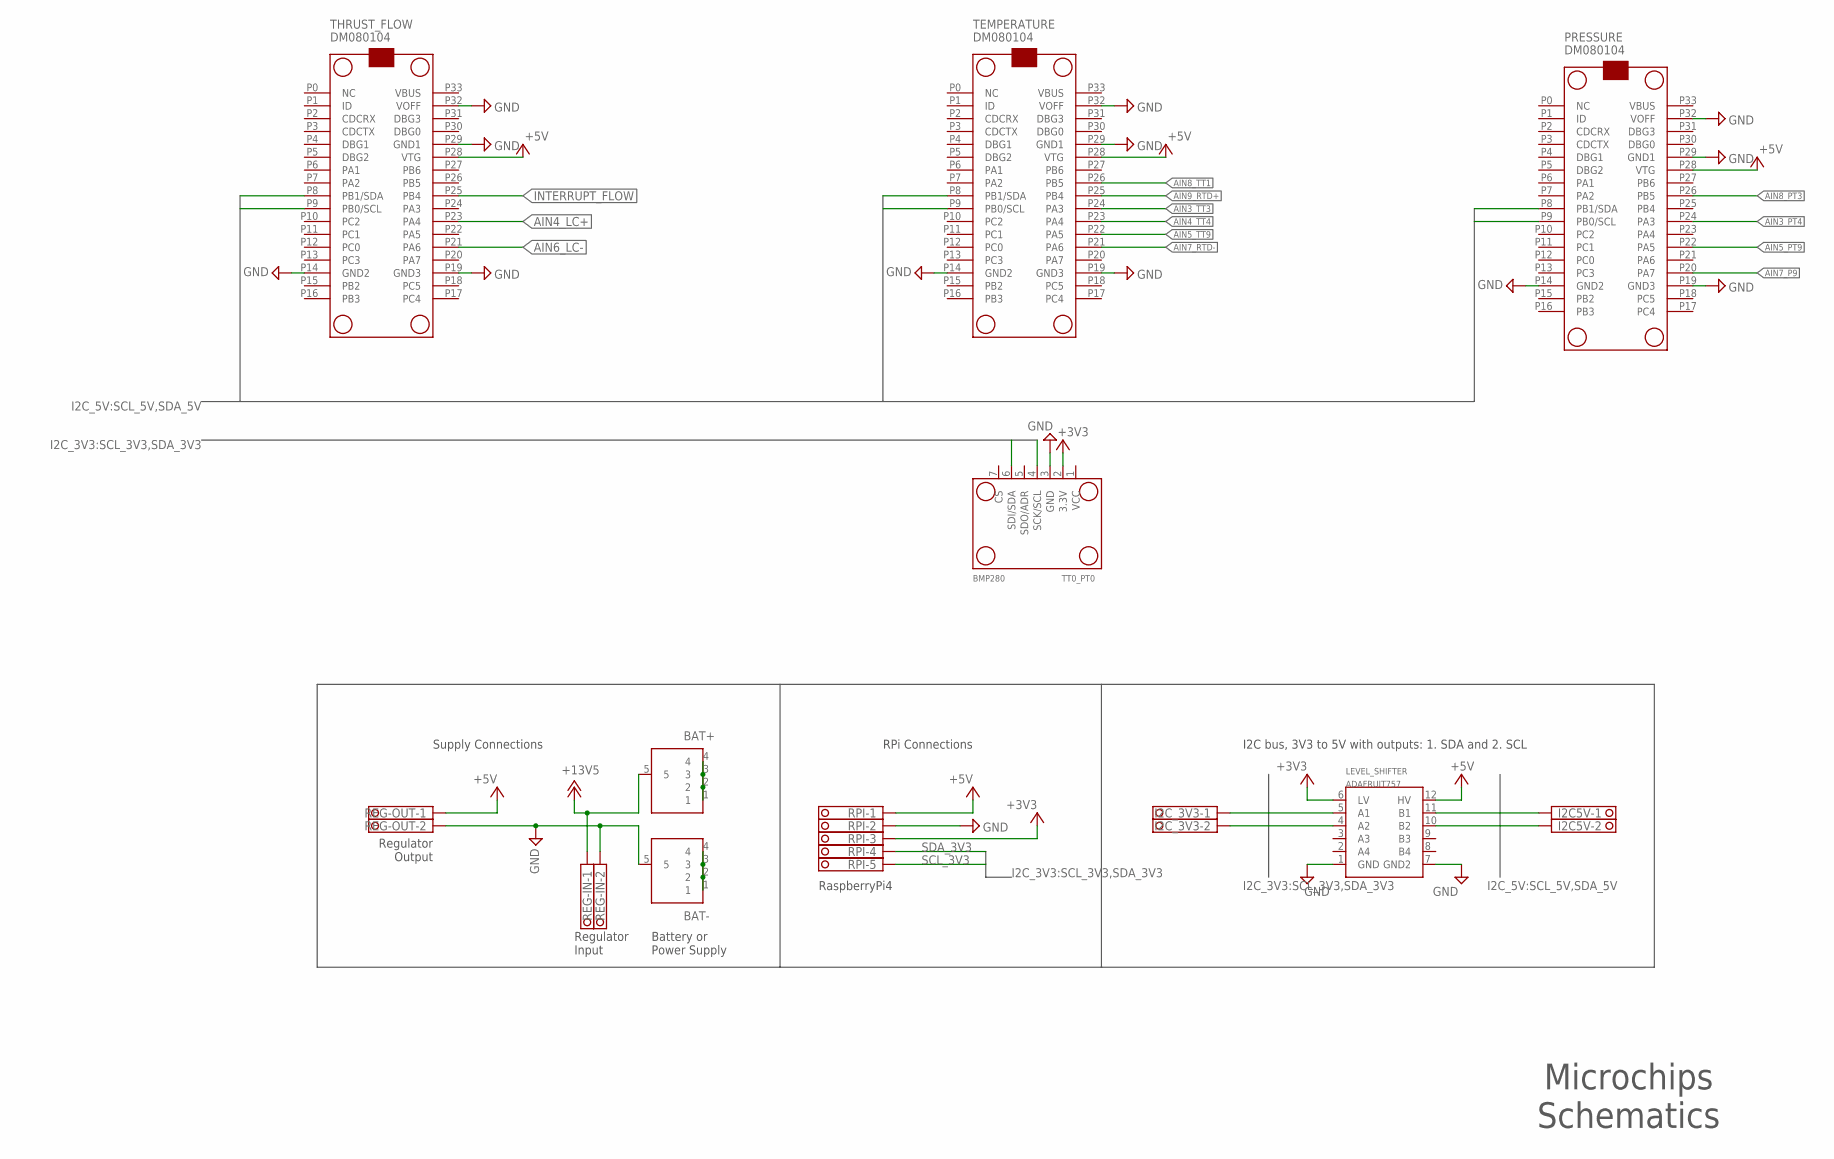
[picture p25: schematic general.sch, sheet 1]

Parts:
BAT+: 73099-2730990; 730990
BAT-: 73099-0; 730990
I2C5V, I2C_3V3: 1751248
LEVEL_SHIFTER: ADAFRUIT757
PRESSURE: DM080104
REG-IN: 1751248
REG-OUT: 1751248
RPI: 1751277
TEMPERATURE: DM080104
THRUST_FLOW: DM080104
TT0_PT0: BMP280

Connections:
+3V3: LEVEL_SHIFTER.6 (LV), RPI.3, TT0_PT0.2 (3.3V); also elsewhere on the board
+5V: LEVEL_SHIFTER.12 (HV), PRESSURE.P28 (VTG), REG-OUT.1, RPI.1, TEMPERATURE.P28 (VTG), THRUST_FLOW.P28 (VTG); also elsewhere on the board
+13V5: BAT+.5, REG-IN.1; also elsewhere on the board
AIN3_PT4: PRESSURE.P24 (PA3); also elsewhere on the board
AIN3_TT3: TEMPERATURE.P24 (PA3); also elsewhere on the board
AIN4_LC+: THRUST_FLOW.P23 (PA4); also elsewhere on the board
AIN4_TT4: TEMPERATURE.P23 (PA4); also elsewhere on the board
AIN5_PT9: PRESSURE.P22 (PA5); also elsewhere on the board
AIN5_TT9: TEMPERATURE.P22 (PA5); also elsewhere on the board
AIN6_LC-: THRUST_FLOW.P21 (PA6); also elsewhere on the board
AIN7_P9: PRESSURE.P20 (PA7); also elsewhere on the board
AIN7_RTD-: TEMPERATURE.P21 (PA6); also elsewhere on the board
AIN8_PT3: PRESSURE.P26 (PB5); also elsewhere on the board
AIN8_TT1: TEMPERATURE.P26 (PB5); also elsewhere on the board
AIN9_RTD+: TEMPERATURE.P25 (PB4); also elsewhere on the board
GND: BAT-.5, LEVEL_SHIFTER.1 (GND), LEVEL_SHIFTER.7 (GND2), PRESSURE.P14 (GND2), PRESSURE.P19 (GND3), PRESSURE.P29 (GND1), PRESSURE.P32 (VOFF), REG-IN.2, REG-OUT.2, RPI.2, TEMPERATURE.P14 (GND2), TEMPERATURE.P19 (GND3), TEMPERATURE.P29 (GND1), TEMPERATURE.P32 (VOFF), THRUST_FLOW.P14 (GND2), THRUST_FLOW.P19 (GND3), THRUST_FLOW.P29 (GND1), THRUST_FLOW.P32 (VOFF), TT0_PT0.3 (GND); also elsewhere on the board
INTERRUPT_FLOW: THRUST_FLOW.P25 (PB4); also elsewhere on the board
unnamed: BAT+.1, BAT+.2, BAT+.3, BAT+.4
unnamed: BAT-.1, BAT-.2, BAT-.3, BAT-.4
SCL_3V3: I2C_3V3.2, LEVEL_SHIFTER.4 (A2), RPI.5, TT0_PT0.4 (SCK/SCL); also elsewhere on the board
SCL_5V: I2C5V.2, LEVEL_SHIFTER.10 (B2), PRESSURE.P9 (PB0/SCL), TEMPERATURE.P9 (PB0/SCL), THRUST_FLOW.P9 (PB0/SCL)
SDA_3V3: I2C_3V3.1, LEVEL_SHIFTER.5 (A1), RPI.4, TT0_PT0.6 (SDI/SDA); also elsewhere on the board
SDA_5V: I2C5V.1, LEVEL_SHIFTER.11 (B1), PRESSURE.P8 (PB1/SDA), TEMPERATURE.P8 (PB1/SDA), THRUST_FLOW.P8 (PB1/SDA)

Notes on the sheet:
I2C bus, 3V3 to 5V with outputs: 1. SDA and 2. SCL
Supply Connections
Microchips Schematics
RPi Connections
Regulator Output
Battery or Power Supply
RaspberryPi4
Regulator Input

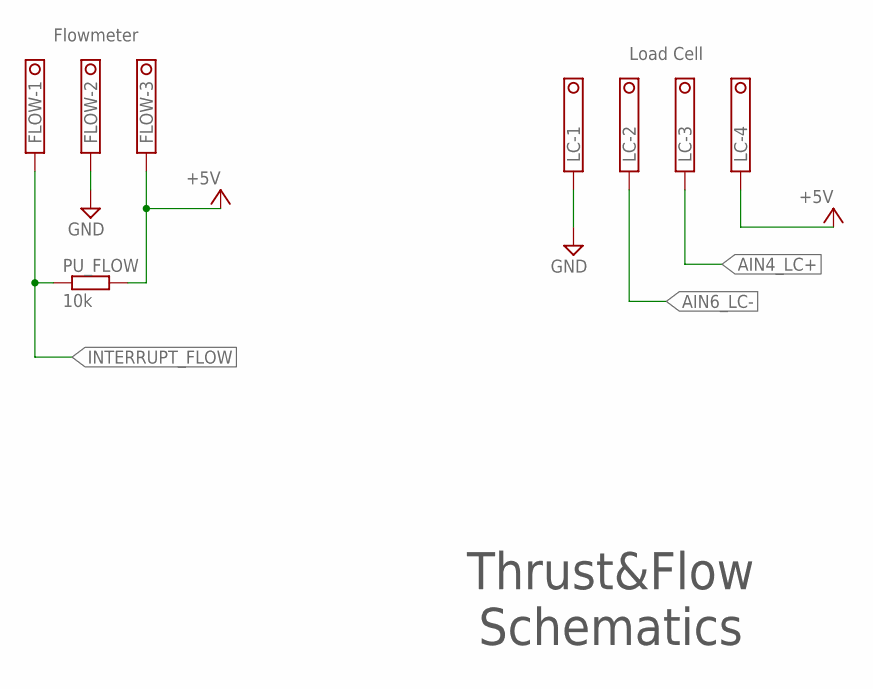
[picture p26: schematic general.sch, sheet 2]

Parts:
FLOW: 1751251
LC: 1751264
PU_FLOW: 10k; 0207/10

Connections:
+5V: FLOW.3, LC.4, PU_FLOW.2; also elsewhere on the board
AIN4_LC+: LC.3; also elsewhere on the board
AIN6_LC-: LC.2; also elsewhere on the board
GND: FLOW.2, LC.1; also elsewhere on the board
INTERRUPT_FLOW: FLOW.1, PU_FLOW.1; also elsewhere on the board

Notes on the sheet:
Thrust&Flow Schematics
Flowmeter
Load Cell

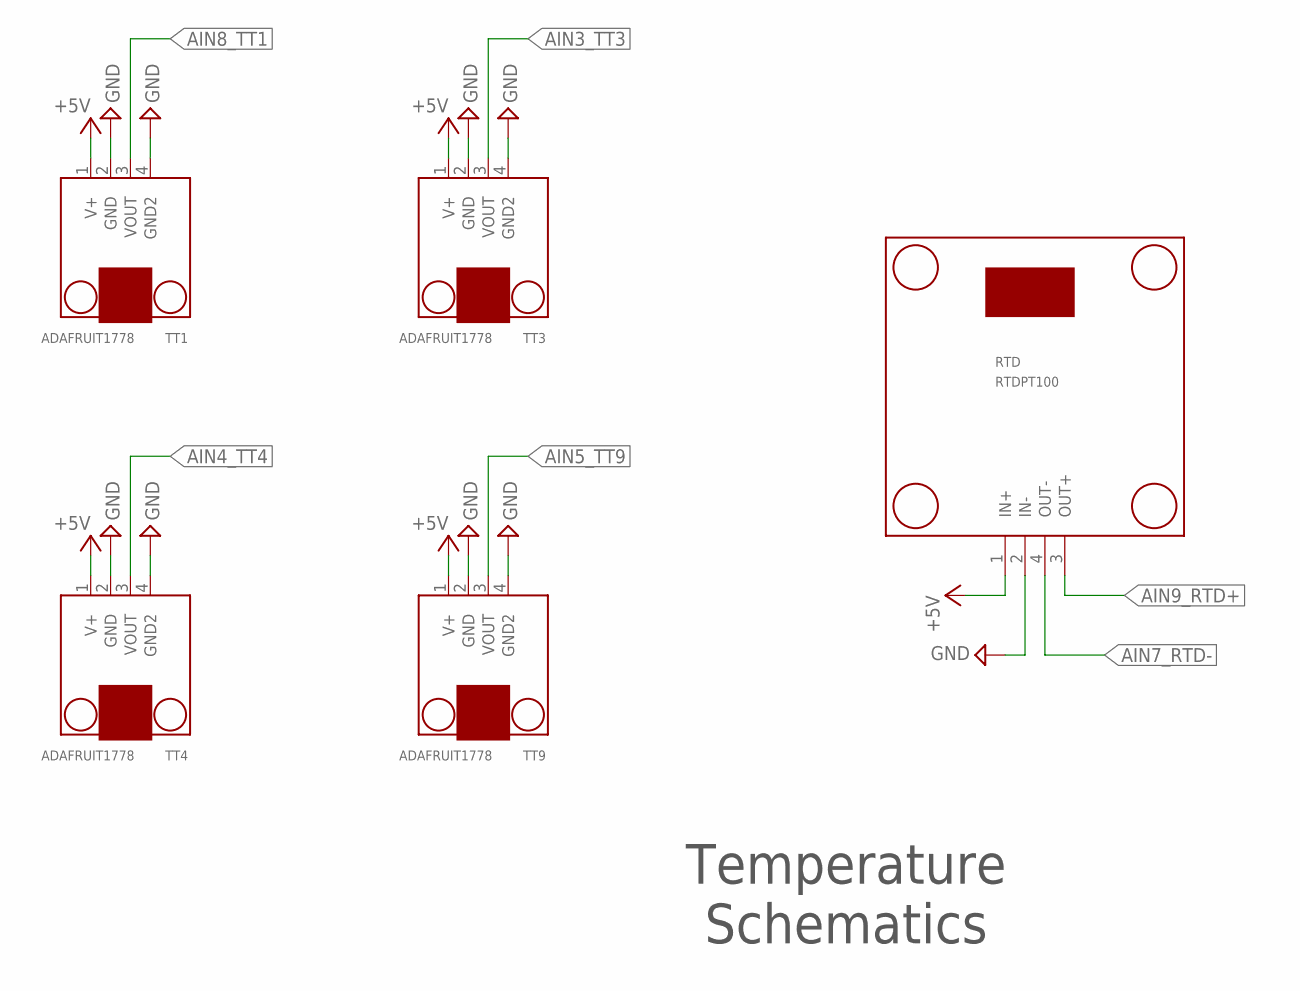
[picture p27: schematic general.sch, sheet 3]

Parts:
RTD: RTDPT100
TT1, TT3, TT4, TT9: ADAFRUIT1778

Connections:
+5V: RTD.1 (IN+), TT1.1 (V+), TT3.1 (V+), TT4.1 (V+), TT9.1 (V+); also elsewhere on the board
AIN3_TT3: TT3.3 (VOUT); also elsewhere on the board
AIN4_TT4: TT4.3 (VOUT); also elsewhere on the board
AIN5_TT9: TT9.3 (VOUT); also elsewhere on the board
AIN7_RTD-: RTD.4 (OUT-); also elsewhere on the board
AIN8_TT1: TT1.3 (VOUT); also elsewhere on the board
AIN9_RTD+: RTD.3 (OUT+); also elsewhere on the board
GND: RTD.2 (IN-), TT1.2 (GND), TT1.4 (GND2), TT3.2 (GND), TT3.4 (GND2), TT4.2 (GND), TT4.4 (GND2), TT9.2 (GND), TT9.4 (GND2); also elsewhere on the board

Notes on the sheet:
Temperature Schematics

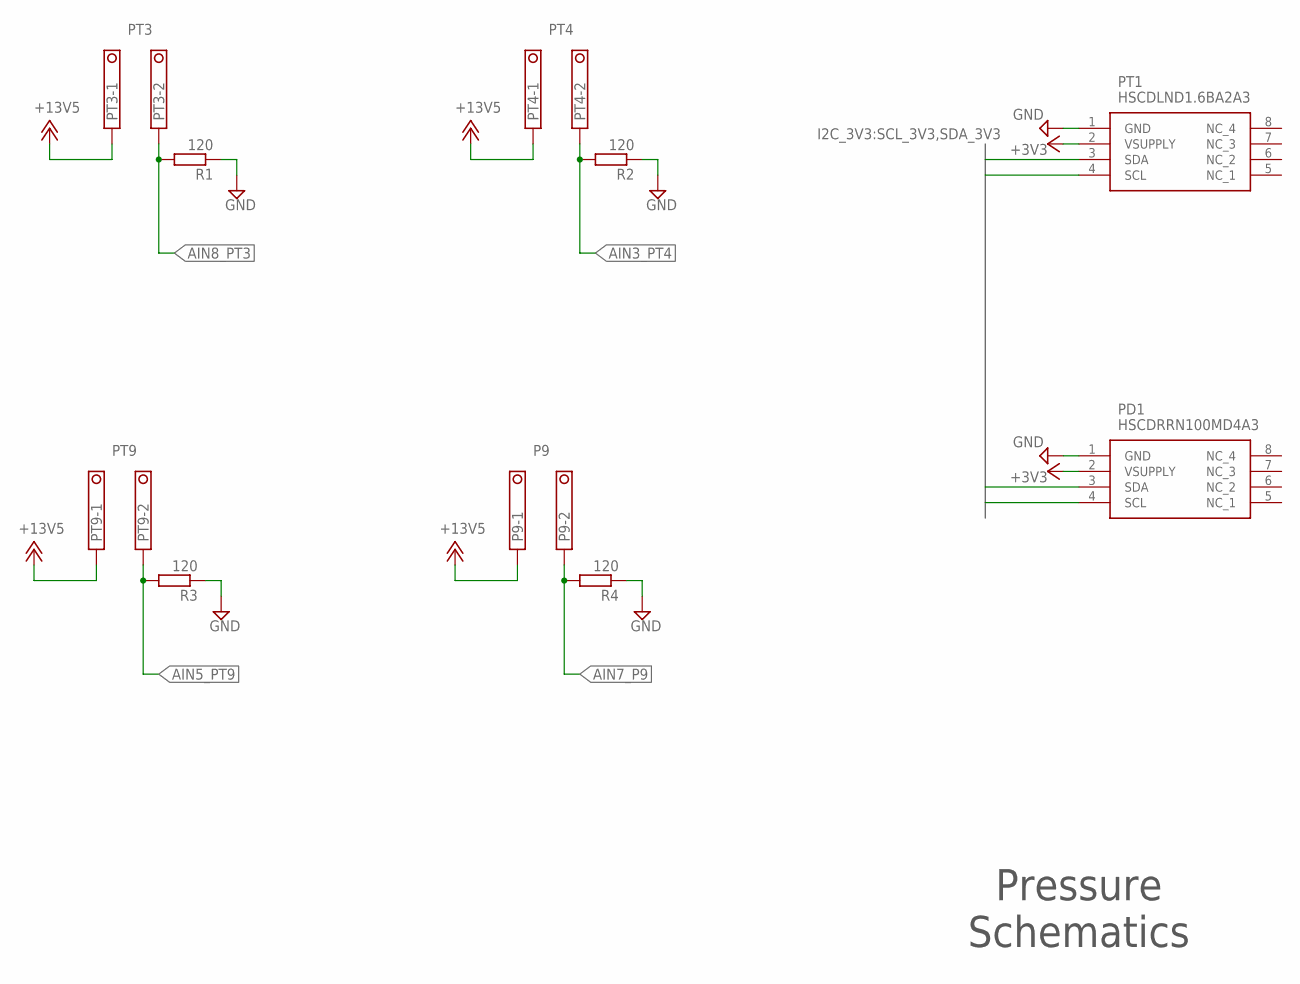
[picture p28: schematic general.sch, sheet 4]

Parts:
P9: 1751248
PD1: HSCDRRN100MD4A3
PT1: HSCDLND1.6BA2A3
PT3, PT4, PT9: 1751248
R1, R2, R3, R4: 120; 0207/10

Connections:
+3V3: PD1.2 (VSUPPLY), PT1.2 (VSUPPLY); also elsewhere on the board
+13V5: P9.1, PT3.1, PT4.1, PT9.1; also elsewhere on the board
AIN3_PT4: PT4.2, R2.2; also elsewhere on the board
AIN5_PT9: PT9.2, R3.2; also elsewhere on the board
AIN7_P9: P9.2, R4.2; also elsewhere on the board
AIN8_PT3: PT3.2, R1.2; also elsewhere on the board
GND: PD1.1 (GND), PT1.1 (GND), R1.1, R2.1, R3.1, R4.1; also elsewhere on the board
SCL_3V3: PD1.4 (SCL), PT1.4 (SCL); also elsewhere on the board
SDA_3V3: PD1.3 (SDA), PT1.3 (SDA); also elsewhere on the board

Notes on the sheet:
Pressure Schematics
PT3
PT4
PT9

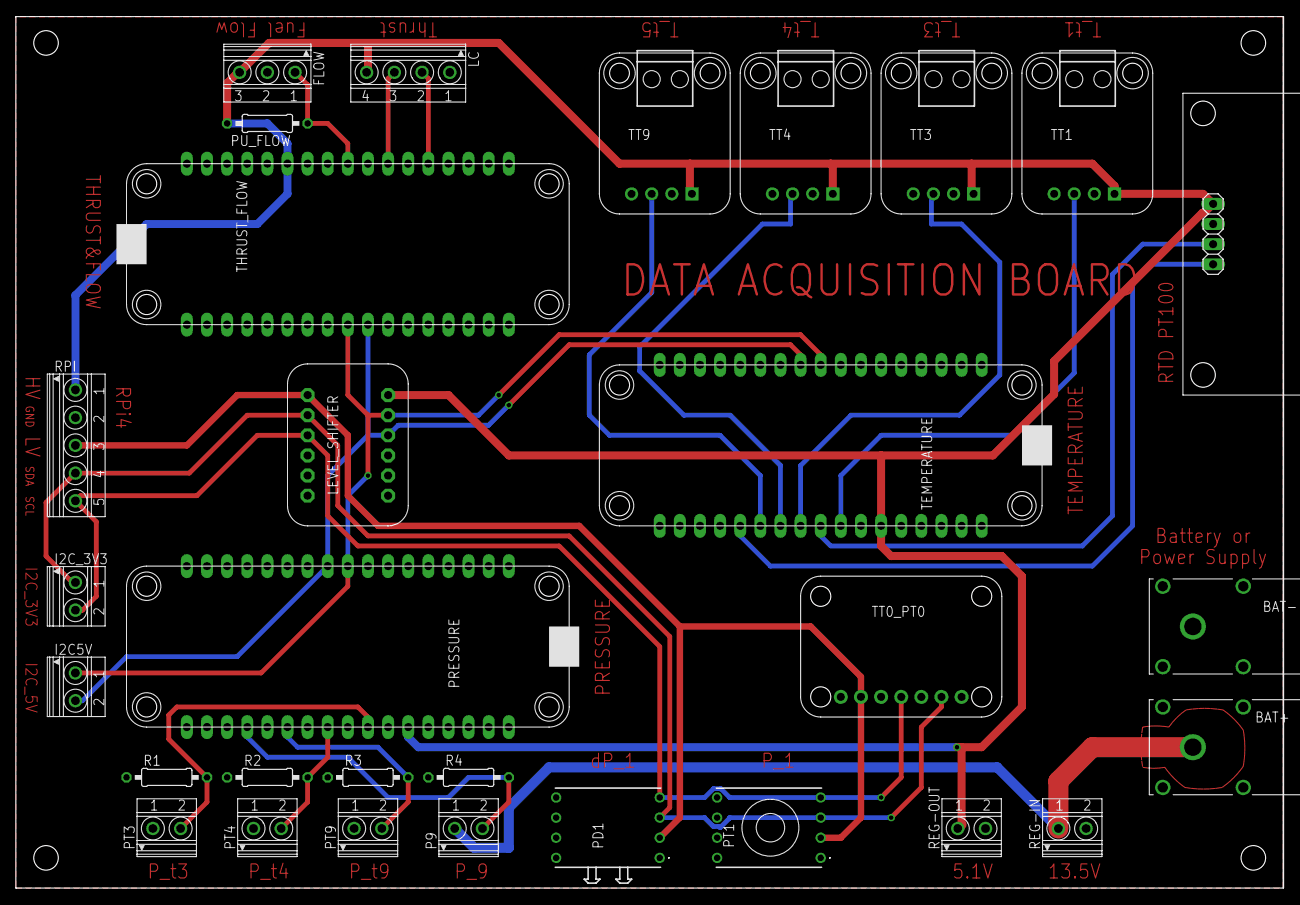
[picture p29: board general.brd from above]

Board: 2 copper layers, 160.0 x 110.0 mm, 30 parts (0 on the bottom side), 23 nets.

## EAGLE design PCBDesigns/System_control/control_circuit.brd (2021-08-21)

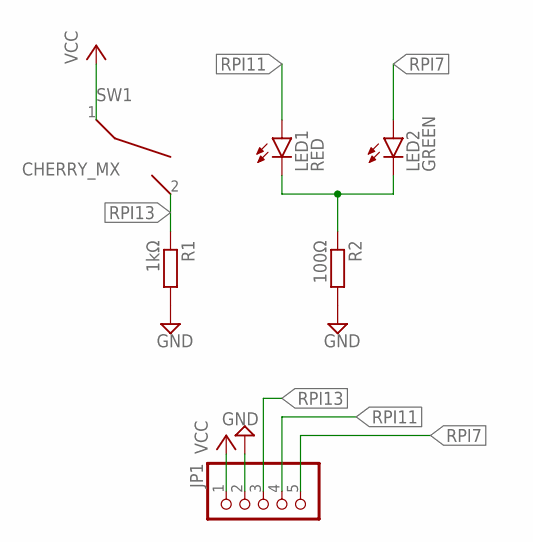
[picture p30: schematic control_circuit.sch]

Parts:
JP1: PINHD-1X5; 1X05
LED1: RED; LED5MM
LED2: GREEN; LED5MM
R1: 1kΩ; 0207/10
R2: 100Ω; 0207/10
SW1: CHERRY_MX; MX1A-XXNN

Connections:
GND: JP1.2, R1.2, R2.2
unnamed: LED1.K (C), LED2.K (C), R2.1
RPI7: JP1.5, LED2.A
RPI11: JP1.4, LED1.A
RPI13: JP1.3, R1.1, SW1.2
VCC: JP1.1, SW1.1

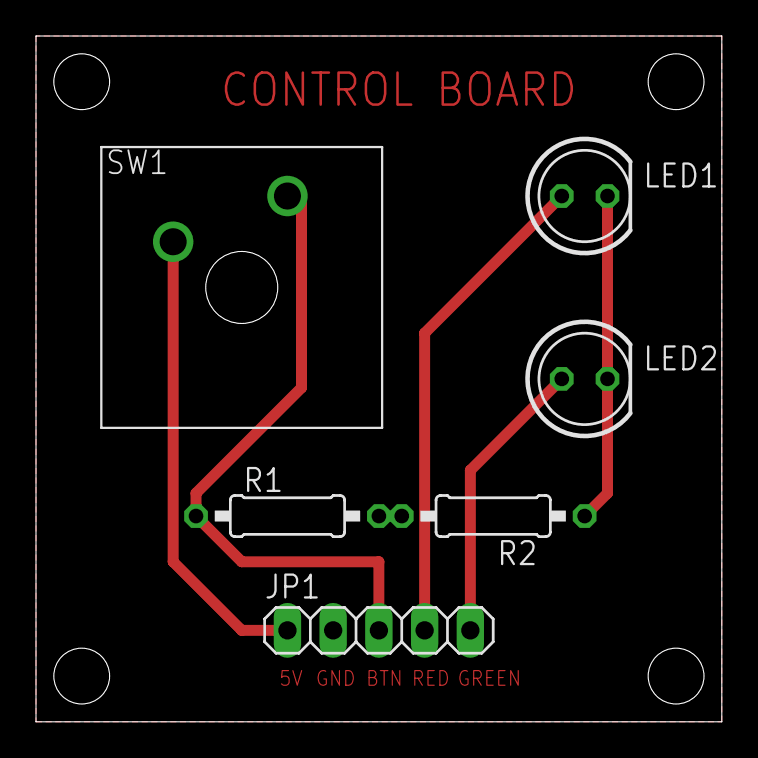
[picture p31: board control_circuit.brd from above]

Board: 2 copper layers, 38.1 x 38.1 mm, 6 parts (0 on the bottom side), 6 nets.

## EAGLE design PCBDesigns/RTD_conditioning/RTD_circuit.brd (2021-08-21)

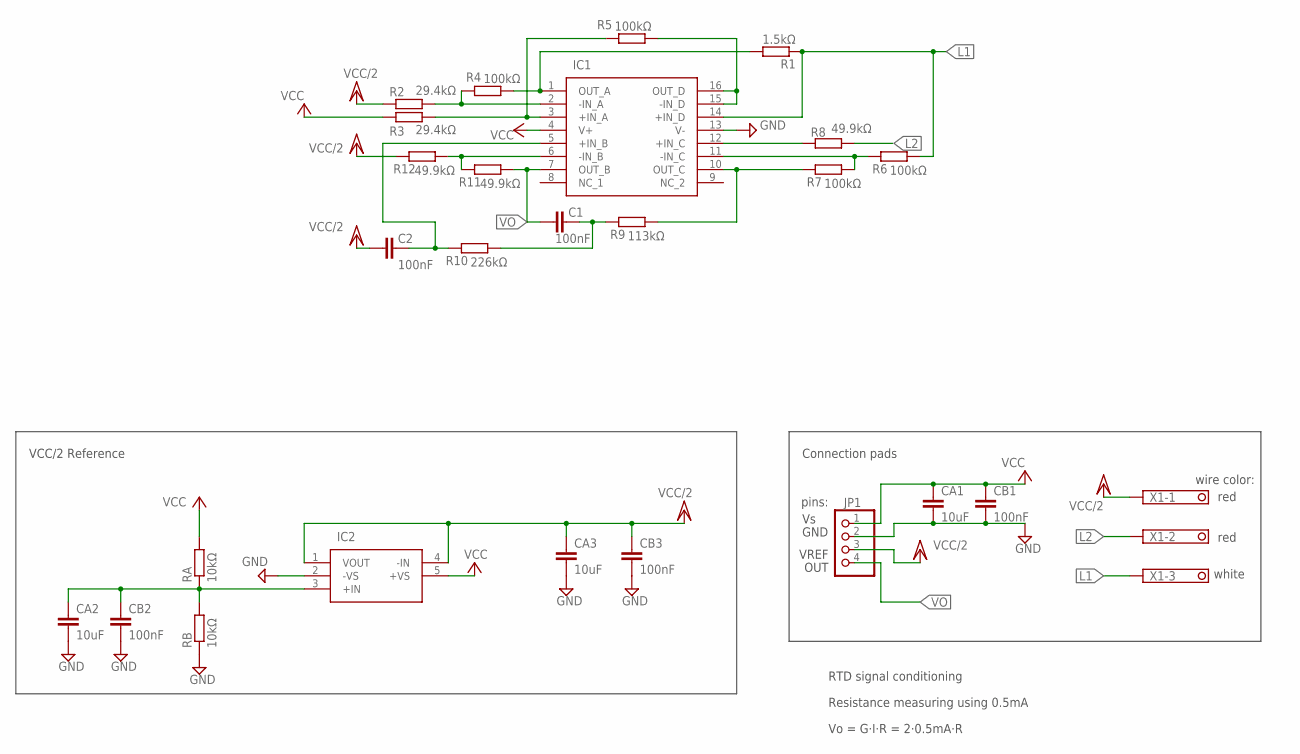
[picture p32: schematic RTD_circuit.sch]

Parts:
C1, C2: 100nF; C0603
CA1, CA2, CA3: 10uF; C0603
CB1, CB2, CB3: 100nF; C0603
IC1: LT1079SW#PBF; SOIC127P1032X264-16N
IC2: AD8031ARTZ-R2; SOT95P280X145-5N
JP1: PINHD-1X4; 1X04
R1: 1.5kΩ; R0603
R2, R3: 29.4kΩ; R0603
R4, R5, R6, R7: 100kΩ; R0603
R8, R11, R12: 49.9kΩ; R0603
R9: 113kΩ; R0603
R10: 226kΩ; R0603
RA: 10kΩ; R0603
RB: 10kΩ; R0603
X1: 1751251

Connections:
DIVIDER: CA2.1, CB2.1, IC2.3 (+IN), RA.1, RB.2
GND: CA1.2, CA2.2, CA3.2, CB1.2, CB2.2, CB3.2, IC1.13 (V-), IC2.2 (-VS), JP1.2, RB.1
L1: IC1.14 (+IN_D), R1.1, R6.1, X1.3
L2: R8.1, X1.2
unnamed: IC1.12 (+IN_C), R8.2
unnamed: IC1.6 (-IN_B), R11.2, R12.1
unnamed: IC1.3 (+IN_A), R3.2, R5.2
unnamed: IC1.2 (-IN_A), R2.2, R4.2
unnamed: IC1.1 (OUT_A), R1.2, R4.1
unnamed: IC1.11 (-IN_C), R6.2, R7.1
unnamed: IC1.15 (-IN_D), IC1.16 (OUT_D), R5.1
unnamed: IC1.10 (OUT_C), R7.2, R9.1
unnamed: C1.1, R9.2, R10.1
unnamed: C2.1, IC1.5 (+IN_B), R10.2
VCC: CA1.1, CB1.1, IC1.4 (V+), IC2.5 (+VS), JP1.1, R3.1, RA.2
VCC/2: C2.2, CA3.1, CB3.1, IC2.1 (VOUT), IC2.4 (-IN), JP1.3, R2.1, R12.2, X1.1
VO: C1.2, IC1.7 (OUT_B), JP1.4, R11.1

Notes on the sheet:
RTD signal conditioning
Resistance measuring using 0.5mA
Vo = G·I·R = 2·0.5mA·R
VCC/2 Reference
wire color:
red
white
Connection pads
pins:
GND
VREF
OUT

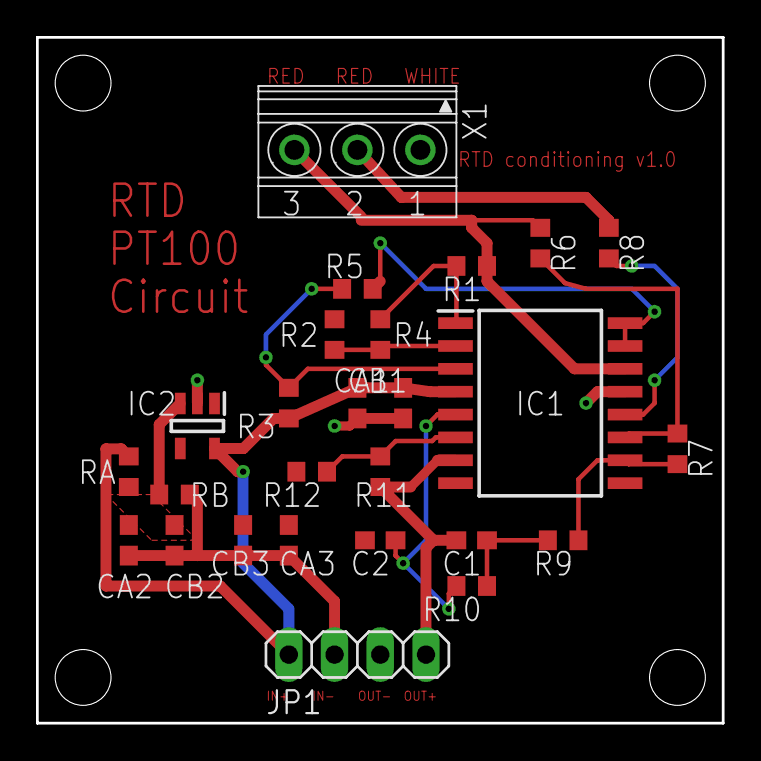
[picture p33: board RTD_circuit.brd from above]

Board: 2 copper layers, 38.1 x 38.1 mm, 26 parts (0 on the bottom side), 17 nets.

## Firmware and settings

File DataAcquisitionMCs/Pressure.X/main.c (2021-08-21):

#include "mcc_generated_files/mcc.h"
#include "transducer.h"

/*
    Main application
*/
int main(void)
{
    /* Initializes MCU, drivers and middleware */
    SYSTEM_Initialize();
    /* Replace with your application code */
    
    Pt3 = 101325.0;
    Pt4 = 101325.0;
    Pt9 = 101325.0;
    P9 = 101325.0;
    
    _delay_ms(500);
    
    while (1){
        
        Pt3 = measure_Pt(3);
        Pt4 = measure_Pt(4);
        Pt9 = measure_Pt(9);
        P9 = measure_Pt(10);
        
        _delay_ms(350);
    }
}
/**
    End of File
*/

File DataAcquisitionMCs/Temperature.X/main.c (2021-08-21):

#include "mcc_generated_files/mcc.h"
#include <util/delay.h>
#include "ADC_toVoltage_Temperature.h"
#include "temperature.h"

/*
    Main application
*/
int main(void)
{
    /* Initializes MCU, drivers and middleware */
    SYSTEM_Initialize();
    
    Tt1 = 268.15;
    Tt3 = 268.15;
    Tt4 = 268.15;
    Tt5 = 268.15;
    
    _delay_ms(500);
    ADC_SetVREF(); //Compute Vref
    
    while (1){

        //thermocouples
        Tt1 = measure_Tt(1);
        Tt4 = measure_Tt(4);
        Tt5 = measure_Tt(9);
        
        //thermocouple or RTD
        bool RTD = false;
        if (RTD)
            Tt3 = measure_Tt(33);
        else
            Tt3 = measure_Tt(3);
        
        ADC_SetVREF(); //monitor supply voltage

        _delay_ms(750);
    }
}
/**
    End of File
*/

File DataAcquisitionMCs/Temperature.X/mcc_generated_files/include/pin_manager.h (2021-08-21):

/**
  @Company
    Microchip Technology Inc.

  @Description
    This Source file provides APIs.
    Generation Information :
    Driver Version    :   1.0.0
*/
/*
    (c) 2018 Microchip Technology Inc. and its subsidiaries. 
    
    Subject to your compliance with these terms, you may use Microchip software and any 
    derivatives exclusively with Microchip products. It is your responsibility to comply with third party 
    license terms applicable to your use of third party software (including open source software) that 
    may accompany Microchip software.
    
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
    IN NO EVENT WILL MICROCHIP BE LIABLE FOR ANY INDIRECT, SPECIAL, PUNITIVE, 
    INCIDENTAL OR CONSEQUENTIAL LOSS, DAMAGE, COST OR EXPENSE OF ANY KIND 
    WHATSOEVER RELATED TO THE SOFTWARE, HOWEVER CAUSED, EVEN IF MICROCHIP 
    HAS BEEN ADVISED OF THE POSSIBILITY OR THE DAMAGES ARE FORESEEABLE. TO 
    THE FULLEST EXTENT ALLOWED BY LAW, MICROCHIP'S TOTAL LIABILITY ON ALL 
    CLAIMS IN ANY WAY RELATED TO THIS SOFTWARE WILL NOT EXCEED THE AMOUNT 
    OF FEES, IF ANY, THAT YOU HAVE PAID DIRECTLY TO MICROCHIP FOR THIS 
    SOFTWARE.
*/

#ifndef PINS_H_INCLUDED
#define PINS_H_INCLUDED

#include <avr/io.h>
#include "port.h"

//get/set PA4 aliases
#define PA4_SetHigh() do { PORTA_OUTSET = 0x10; } while(0)
#define PA4_SetLow() do { PORTA_OUTCLR = 0x10; } while(0)
#define PA4_Toggle() do { PORTA_OUTTGL = 0x10; } while(0)
#define PA4_GetValue() (VPORTA.IN & (0x1 << 4))
#define PA4_SetDigitalInput() do { PORTA_DIRCLR = 0x10; } while(0)
#define PA4_SetDigitalOutput() do { PORTA_DIRSET = 0x10; } while(0)
#define PA4_SetPullUp() do { PORTA_PIN4CTRL  |= PORT_PULLUPEN_bm; } while(0)
#define PA4_ResetPullUp() do { PORTA_PIN4CTRL  &= ~PORT_PULLUPEN_bm; } while(0)
#define PA4_SetInverted() do { PORTA_PIN4CTRL  |= PORT_INVEN_bm; } while(0)
#define PA4_ResetInverted() do { PORTA_PIN4CTRL  &= ~PORT_INVEN_bm; } while(0)
#define PA4_DisableInterruptOnChange() do { PORTA.PIN4CTRL = (PORTA.PIN4CTRL & ~PORT_ISC_gm) | 0x0 ; } while(0)
#define PA4_EnableInterruptForBothEdges() do { PORTA.PIN4CTRL = (PORTA.PIN4CTRL & ~PORT_ISC_gm) | 0x1 ; } while(0)
#define PA4_EnableInterruptForRisingEdge() do { PORTA.PIN4CTRL = (PORTA.PIN4CTRL & ~PORT_ISC_gm) | 0x2 ; } while(0)
#define PA4_EnableInterruptForFallingEdge() do { PORTA.PIN4CTRL = (PORTA.PIN4CTRL & ~PORT_ISC_gm) | 0x3 ; } while(0)
#define PA4_DisableDigitalInputBuffer() do { PORTA.PIN4CTRL = (PORTA.PIN4CTRL & ~PORT_ISC_gm) | 0x4 ; } while(0)
#define PA4_EnableInterruptForLowLevelSensing() do { PORTA.PIN4CTRL = (PORTA.PIN4CTRL & ~PORT_ISC_gm) | 0x5 ; } while(0)

//get/set PB5 aliases
#define PB5_SetHigh() do { PORTB_OUTSET = 0x20; } while(0)
#define PB5_SetLow() do { PORTB_OUTCLR = 0x20; } while(0)
#define PB5_Toggle() do { PORTB_OUTTGL = 0x20; } while(0)
#define PB5_GetValue() (VPORTB.IN & (0x1 << 5))
#define PB5_SetDigitalInput() do { PORTB_DIRCLR = 0x20; } while(0)
#define PB5_SetDigitalOutput() do { PORTB_DIRSET = 0x20; } while(0)
#define PB5_SetPullUp() do { PORTB_PIN5CTRL  |= PORT_PULLUPEN_bm; } while(0)
#define PB5_ResetPullUp() do { PORTB_PIN5CTRL  &= ~PORT_PULLUPEN_bm; } while(0)
#define PB5_SetInverted() do { PORTB_PIN5CTRL  |= PORT_INVEN_bm; } while(0)
#define PB5_ResetInverted() do { PORTB_PIN5CTRL  &= ~PORT_INVEN_bm; } while(0)
#define PB5_DisableInterruptOnChange() do { PORTB.PIN5CTRL = (PORTB.PIN5CTRL & ~PORT_ISC_gm) | 0x0 ; } while(0)
#define PB5_EnableInterruptForBothEdges() do { PORTB.PIN5CTRL = (PORTB.PIN5CTRL & ~PORT_ISC_gm) | 0x1 ; } while(0)
#define PB5_EnableInterruptForRisingEdge() do { PORTB.PIN5CTRL = (PORTB.PIN5CTRL & ~PORT_ISC_gm) | 0x2 ; } while(0)
#define PB5_EnableInterruptForFallingEdge() do { PORTB.PIN5CTRL = (PORTB.PIN5CTRL & ~PORT_ISC_gm) | 0x3 ; } while(0)
#define PB5_DisableDigitalInputBuffer() do { PORTB.PIN5CTRL = (PORTB.PIN5CTRL & ~PORT_ISC_gm) | 0x4 ; } while(0)
#define PB5_EnableInterruptForLowLevelSensing() do { PORTB.PIN5CTRL = (PORTB.PIN5CTRL & ~PORT_ISC_gm) | 0x5 ; } while(0)

//get/set PA3 aliases
#define PA3_SetHigh() do { PORTA_OUTSET = 0x8; } while(0)
#define PA3_SetLow() do { PORTA_OUTCLR = 0x8; } while(0)
#define PA3_Toggle() do { PORTA_OUTTGL = 0x8; } while(0)
#define PA3_GetValue() (VPORTA.IN & (0x1 << 3))
#define PA3_SetDigitalInput() do { PORTA_DIRCLR = 0x8; } while(0)
#define PA3_SetDigitalOutput() do { PORTA_DIRSET = 0x8; } while(0)
#define PA3_SetPullUp() do { PORTA_PIN3CTRL  |= PORT_PULLUPEN_bm; } while(0)
#define PA3_ResetPullUp() do { PORTA_PIN3CTRL  &= ~PORT_PULLUPEN_bm; } while(0)
#define PA3_SetInverted() do { PORTA_PIN3CTRL  |= PORT_INVEN_bm; } while(0)
#define PA3_ResetInverted() do { PORTA_PIN3CTRL  &= ~PORT_INVEN_bm; } while(0)
#define PA3_DisableInterruptOnChange() do { PORTA.PIN3CTRL = (PORTA.PIN3CTRL & ~PORT_ISC_gm) | 0x0 ; } while(0)
#define PA3_EnableInterruptForBothEdges() do { PORTA.PIN3CTRL = (PORTA.PIN3CTRL & ~PORT_ISC_gm) | 0x1 ; } while(0)
#define PA3_EnableInterruptForRisingEdge() do { PORTA.PIN3CTRL = (PORTA.PIN3CTRL & ~PORT_ISC_gm) | 0x2 ; } while(0)
#define PA3_EnableInterruptForFallingEdge() do { PORTA.PIN3CTRL = (PORTA.PIN3CTRL & ~PORT_ISC_gm) | 0x3 ; } while(0)
#define PA3_DisableDigitalInputBuffer() do { PORTA.PIN3CTRL = (PORTA.PIN3CTRL & ~PORT_ISC_gm) | 0x4 ; } while(0)
#define PA3_EnableInterruptForLowLevelSensing() do { PORTA.PIN3CTRL = (PORTA.PIN3CTRL & ~PORT_ISC_gm) | 0x5 ; } while(0)

//get/set PB4 aliases
#define PB4_SetHigh() do { PORTB_OUTSET = 0x10; } while(0)
#define PB4_SetLow() do { PORTB_OUTCLR = 0x10; } while(0)
#define PB4_Toggle() do { PORTB_OUTTGL = 0x10; } while(0)
#define PB4_GetValue() (VPORTB.IN & (0x1 << 4))
#define PB4_SetDigitalInput() do { PORTB_DIRCLR = 0x10; } while(0)
#define PB4_SetDigitalOutput() do { PORTB_DIRSET = 0x10; } while(0)
#define PB4_SetPullUp() do { PORTB_PIN4CTRL  |= PORT_PULLUPEN_bm; } while(0)
#define PB4_ResetPullUp() do { PORTB_PIN4CTRL  &= ~PORT_PULLUPEN_bm; } while(0)
#define PB4_SetInverted() do { PORTB_PIN4CTRL  |= PORT_INVEN_bm; } while(0)
#define PB4_ResetInverted() do { PORTB_PIN4CTRL  &= ~PORT_INVEN_bm; } while(0)
#define PB4_DisableInterruptOnChange() do { PORTB.PIN4CTRL = (PORTB.PIN4CTRL & ~PORT_ISC_gm) | 0x0 ; } while(0)
#define PB4_EnableInterruptForBothEdges() do { PORTB.PIN4CTRL = (PORTB.PIN4CTRL & ~PORT_ISC_gm) | 0x1 ; } while(0)
#define PB4_EnableInterruptForRisingEdge() do { PORTB.PIN4CTRL = (PORTB.PIN4CTRL & ~PORT_ISC_gm) | 0x2 ; } while(0)
#define PB4_EnableInterruptForFallingEdge() do { PORTB.PIN4CTRL = (PORTB.PIN4CTRL & ~PORT_ISC_gm) | 0x3 ; } while(0)
#define PB4_DisableDigitalInputBuffer() do { PORTB.PIN4CTRL = (PORTB.PIN4CTRL & ~PORT_ISC_gm) | 0x4 ; } while(0)
#define PB4_EnableInterruptForLowLevelSensing() do { PORTB.PIN4CTRL = (PORTB.PIN4CTRL & ~PORT_ISC_gm) | 0x5 ; } while(0)
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

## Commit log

2021-08-21 Structure files
    Added all the files that simulate the test rig structure, included designed parts with drawings.
    [Back_piece.ipt, Base.dwg, Base.dxf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]
2021-08-21 Added master files
    Code files to program a Raspberry Pi 4 as master of the data acquisition system.
2021-08-21 Added PCB designs
    Schematics and board designs of the whole electronic system.
    [RTD_circuit.brd, RTD_circuit.sch, control_circuit.brd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]
2021-08-26 Name change (Union to Mounting)
    Change from:
    Engine_Union to Engine_Mounting
    Union_axis to Mounting_Shaft
    Files:
    Assembly (relationships)
    Part names
    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
    [Engine_Mounting.dwg, Engine_Mounting.dxf, Engine_Mounting.ipt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]
